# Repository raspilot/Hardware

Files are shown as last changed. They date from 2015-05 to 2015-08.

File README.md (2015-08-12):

#树莓派飞控RasPilot#

###RasPilot硬件参数###
特性
* 支持树莓派1 A+/B+；树莓派2 B+
* STM32F103 failsafe co-processor
* ardupilot飞控代码
* pixhawk接口兼容
* USB(RPi) / Servo Rail BEC / Power Module三路电源输入

传感器
* ST Micro L3GD20H 16位陀螺仪
* ST Micro LSM303D 14位加速度计/磁力计
* Invensense MPU 6000 3轴陀螺仪/加速度计
* MEAS MS5611 气压计

接口
* 2x UART
* 1x CAN
* 8x PWM
* Spektrum DSM / DSM2 / DSM-X® Satellite 兼容接收机
* Futaba S.BUS® 兼容输入输出
* PPM sum 接收机
* RSSI（PWM或电压）输入
* 1x I2C
* 3.3V & 6.6V A/D输入
* 安全开关
* 蜂鸣器接口
* 板载三色LED

###硬件安装和接线###
1 安装外壳。如下图，用铜柱和螺母将树莓派固定在底壳上。插上飞控扩展板，再用螺丝固定上壳。<br>

<br>
<br>
2 接口说明：<br>
<br>

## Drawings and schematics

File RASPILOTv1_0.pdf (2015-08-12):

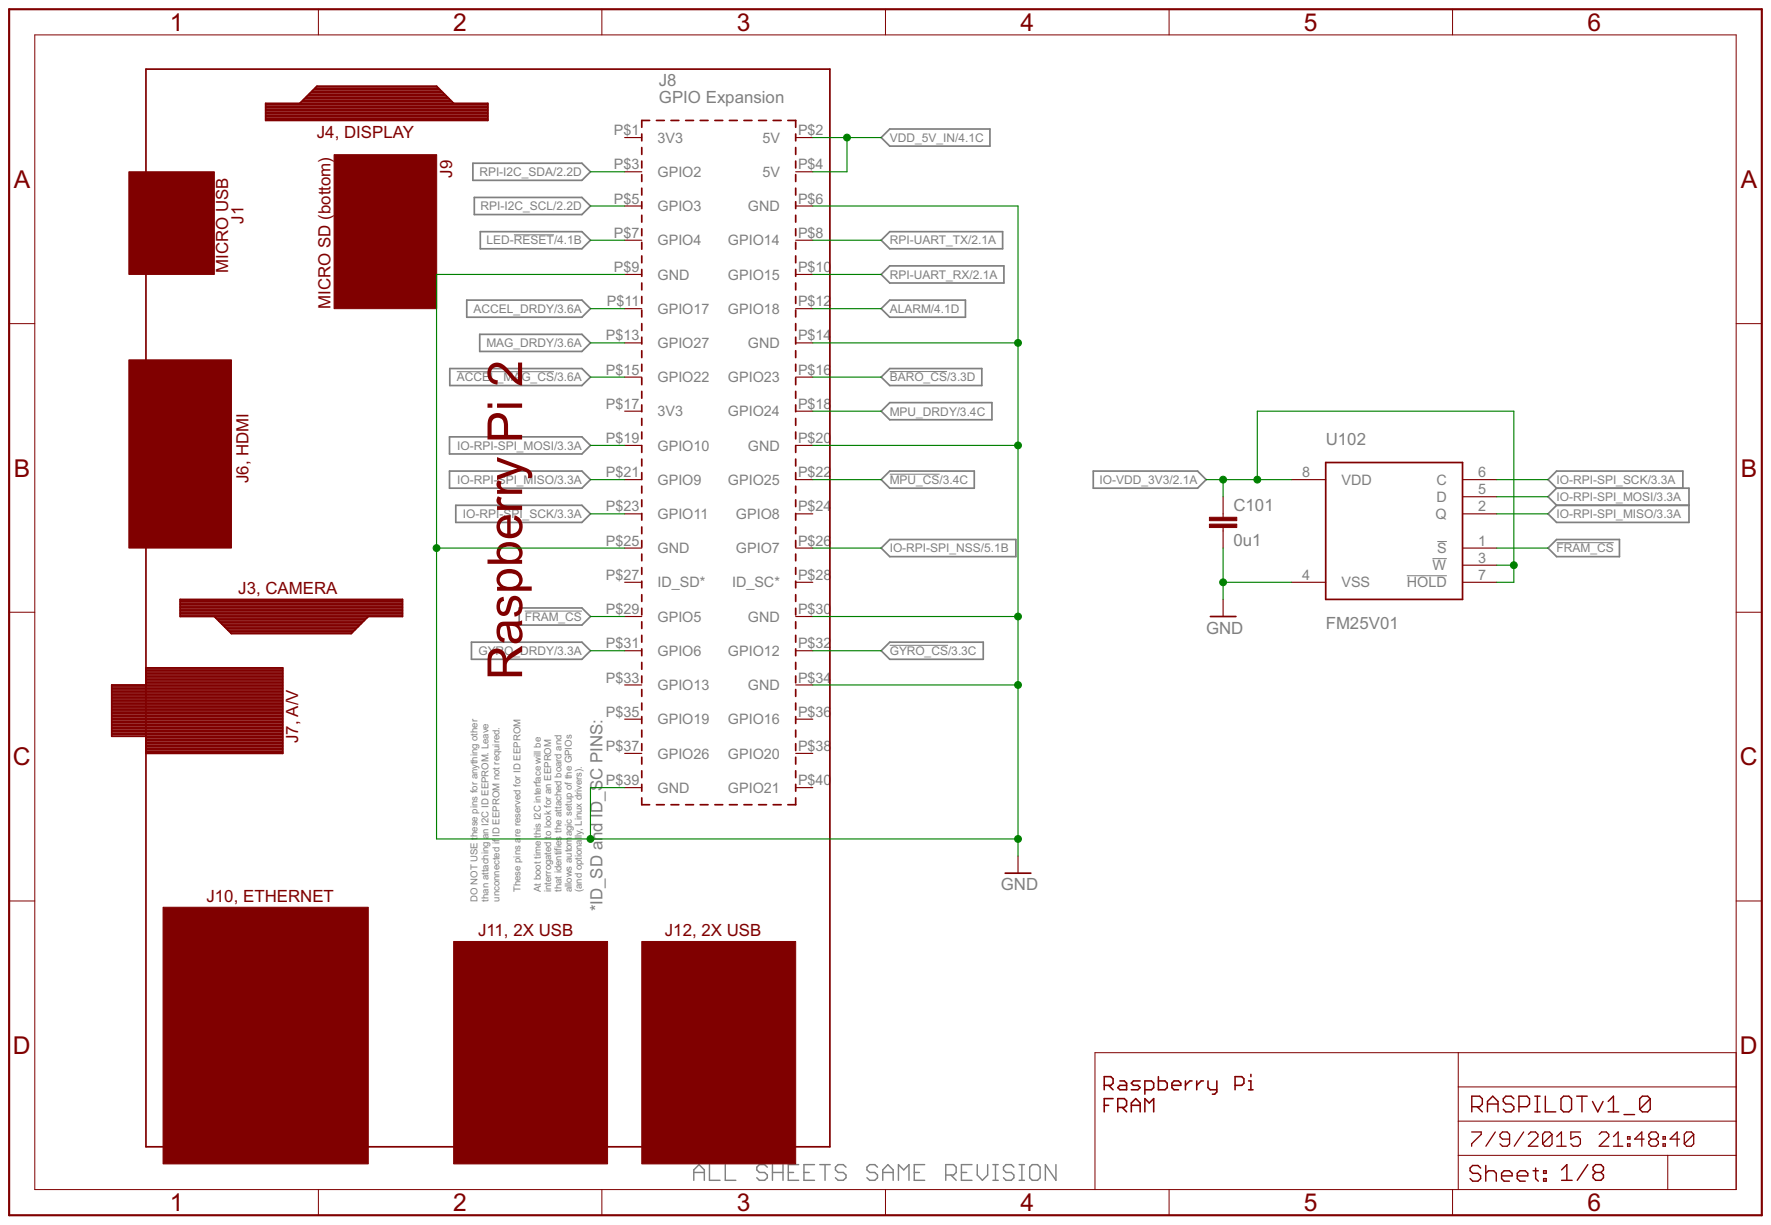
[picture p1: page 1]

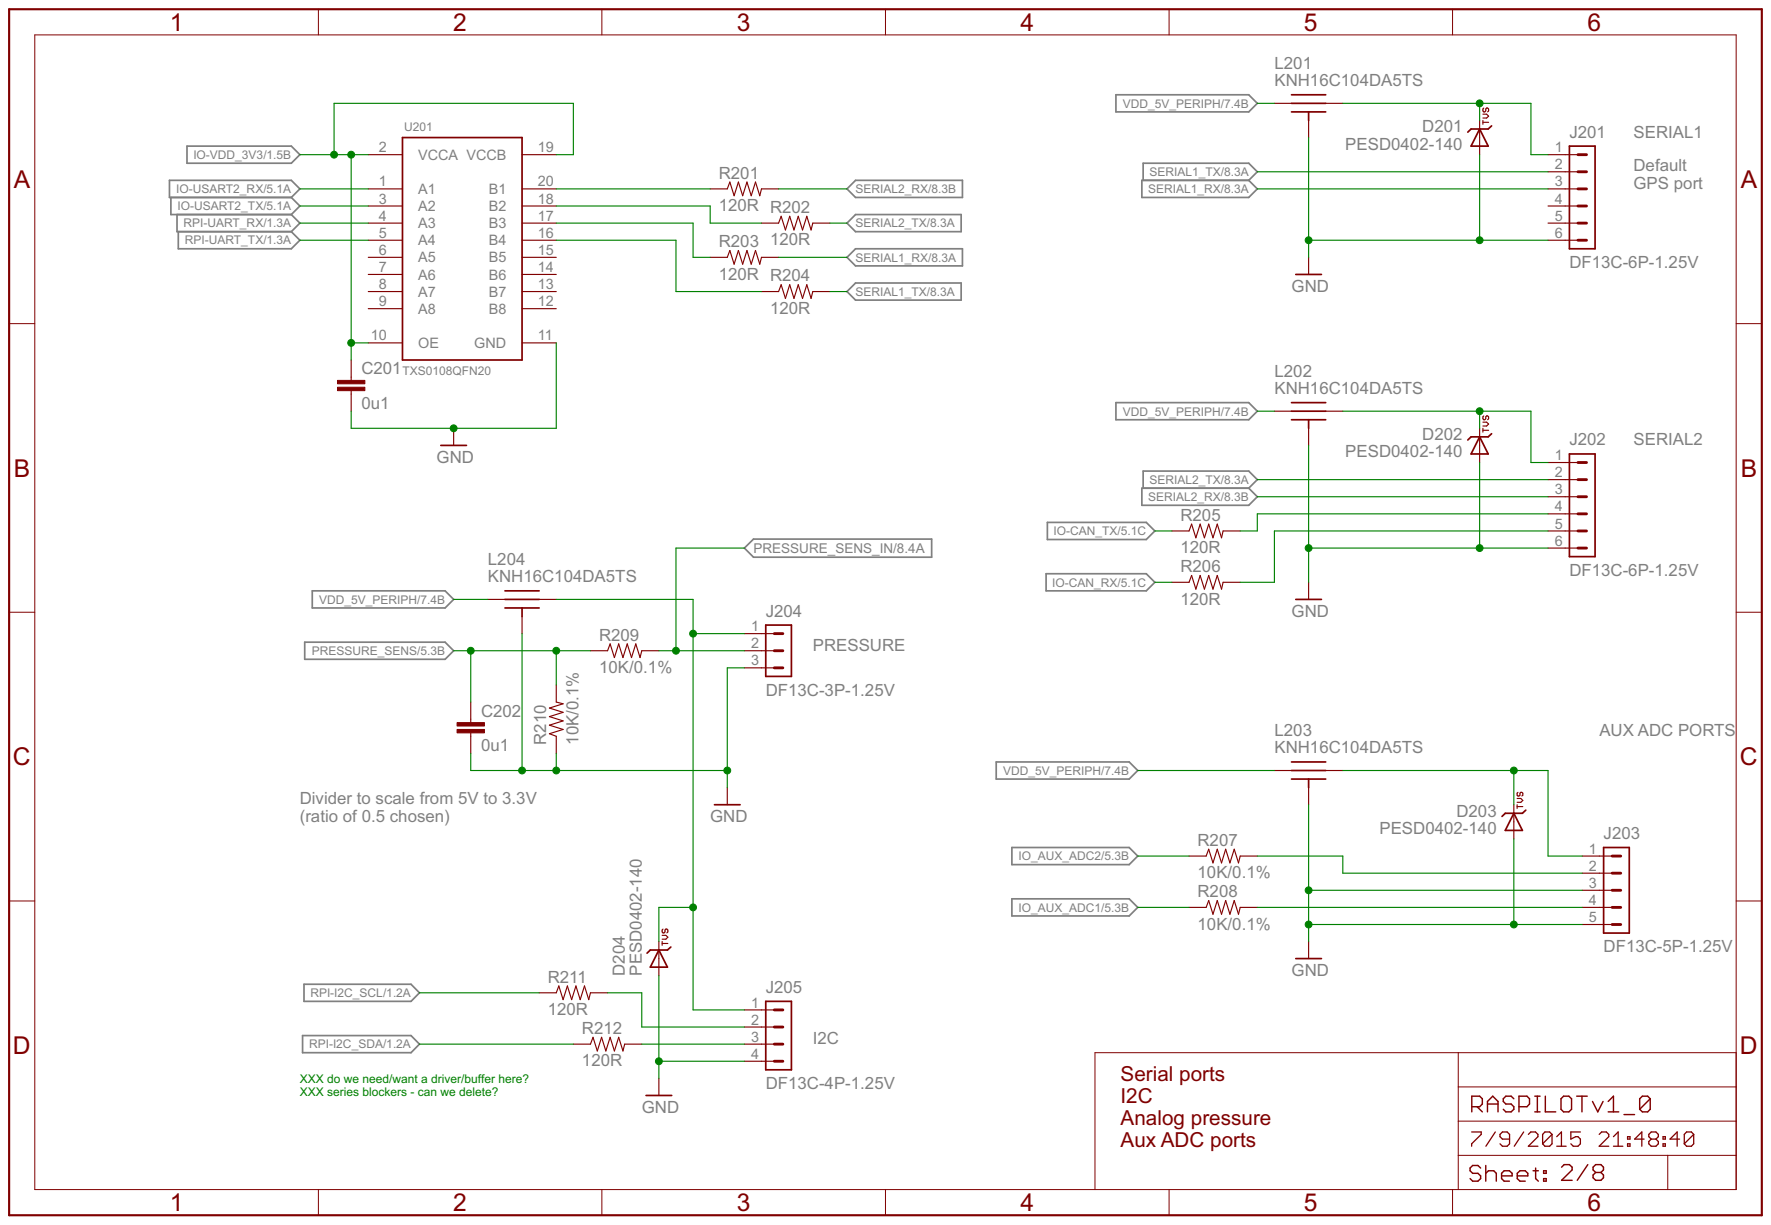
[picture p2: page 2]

Divider to scale from 5V to 3.3V
(ratio of 0.5 chosen)

XXX do we need/want a driver/buffer here? XXX series blockers - can we delete?

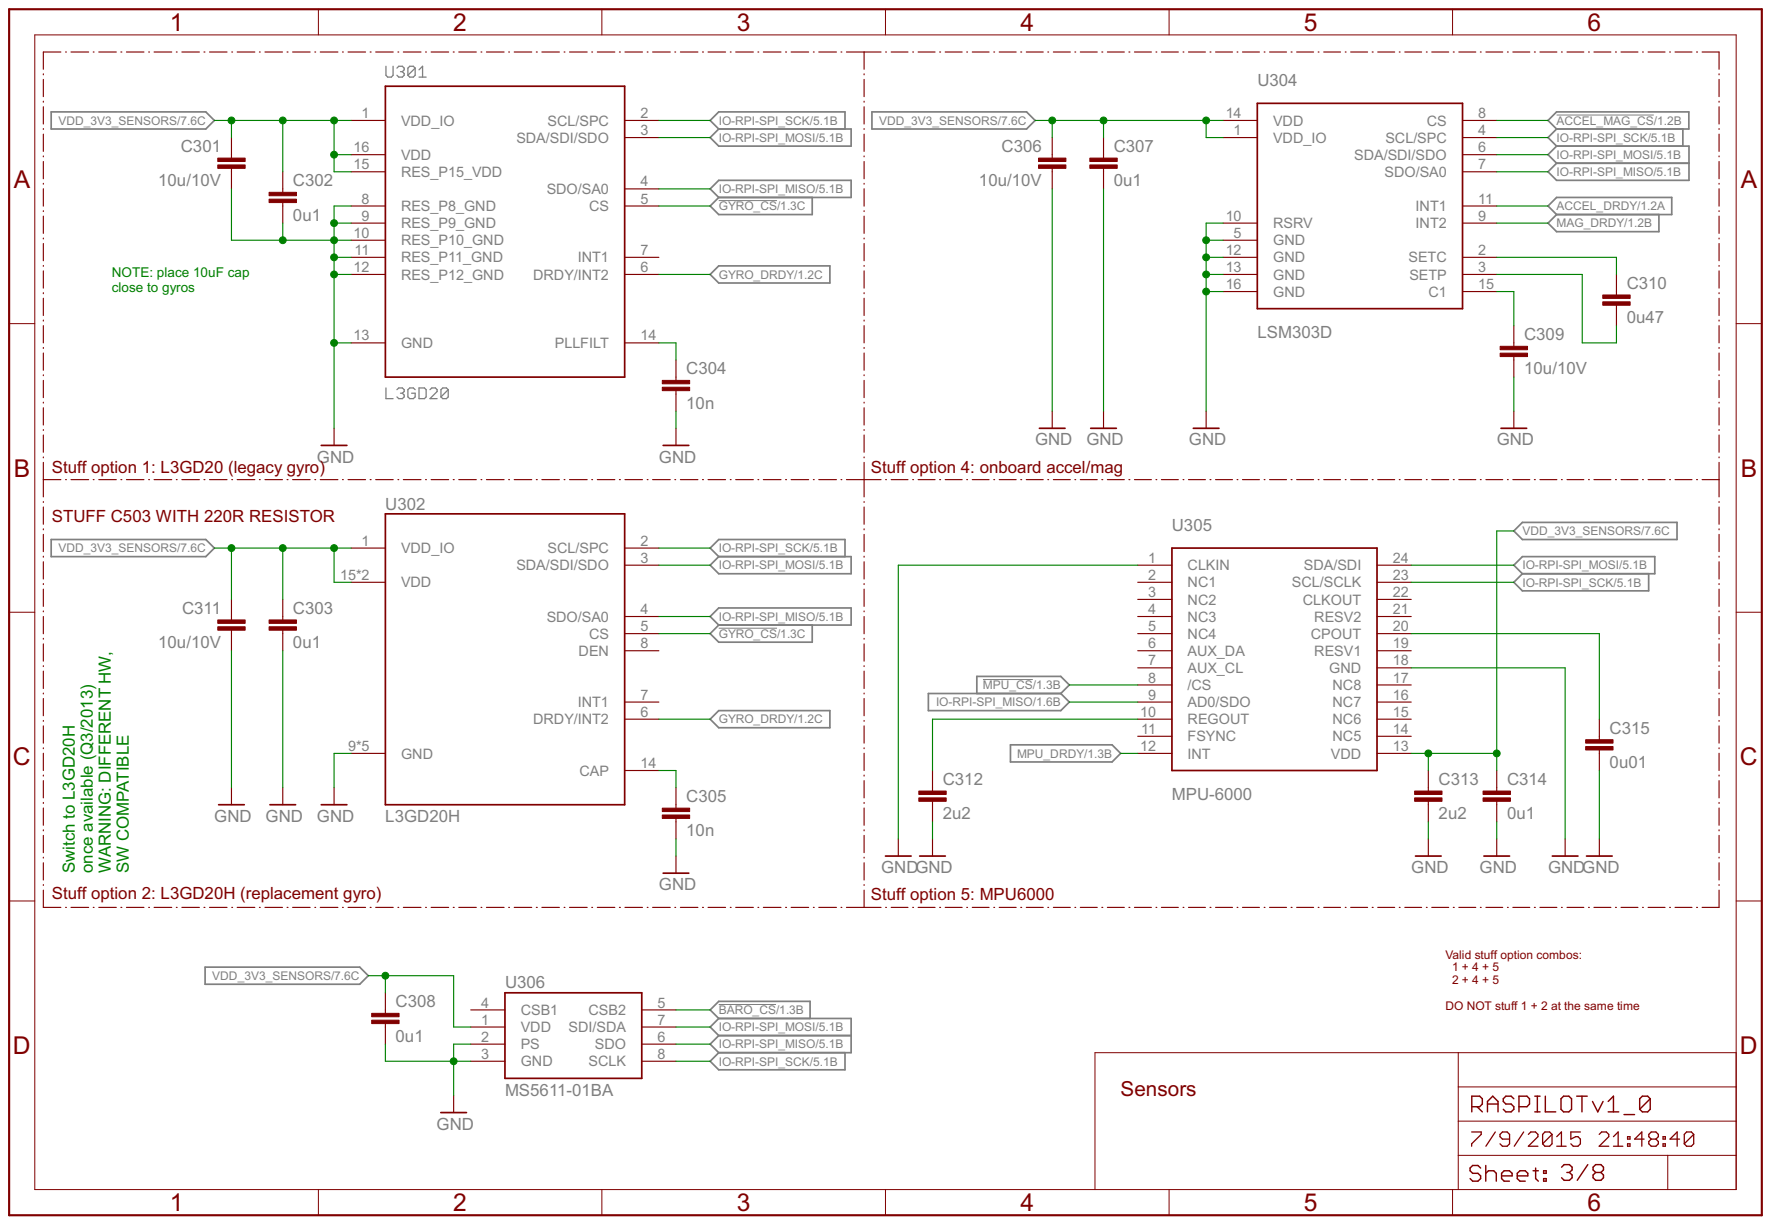
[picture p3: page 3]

Stuff option 1: L3GD20 (legacy gyro)

Stuff option 4: onboard accel/mag

19 CPOUT 18 RESV1

once available (Q3/2013) WARNING: DIFFERENT HW, SW CO

17 GND 16 NC8 15 NC7 14 NC6 13 NC5

Stuff option 2: L3GD20H (replacement gyro)

Valid stuff option combos: 1 + 4 + 5

2 + 4 + 5 DO NOT stuff 1 + 2 at the same time

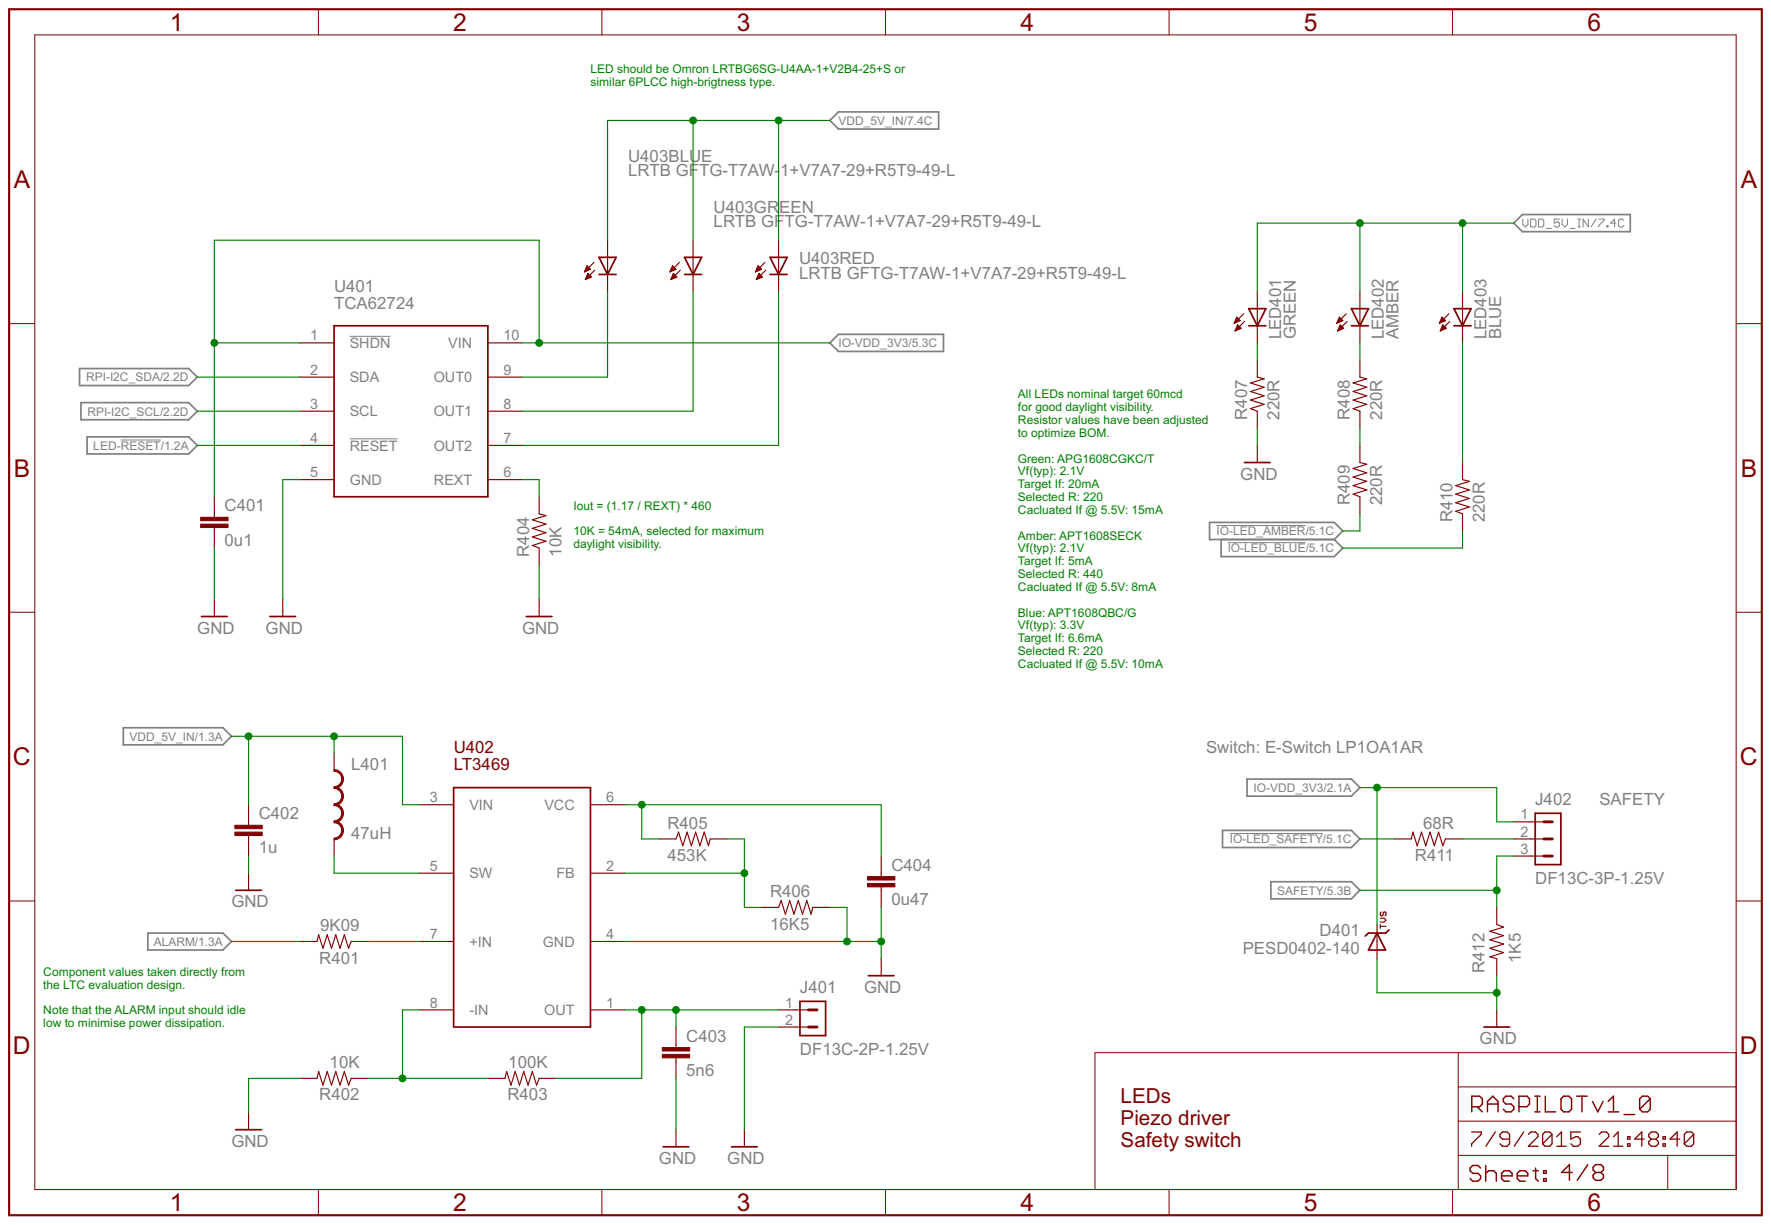
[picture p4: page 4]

LED should be Omron LRTBG6SG-U4AA-1+V2B4-25+S or similar 6PLCC high-brigtness type.

All LEDs nominal target 60mcd
for good daylight visibility. Resistor values have been adjusted

to optimize BOM. Green: APG1608CGKC/T Vf(typ): 2.1V

Component values taken directly from
the LTC evaluation design. Note that the ALARM input should idle

low to minimise power dissipation.

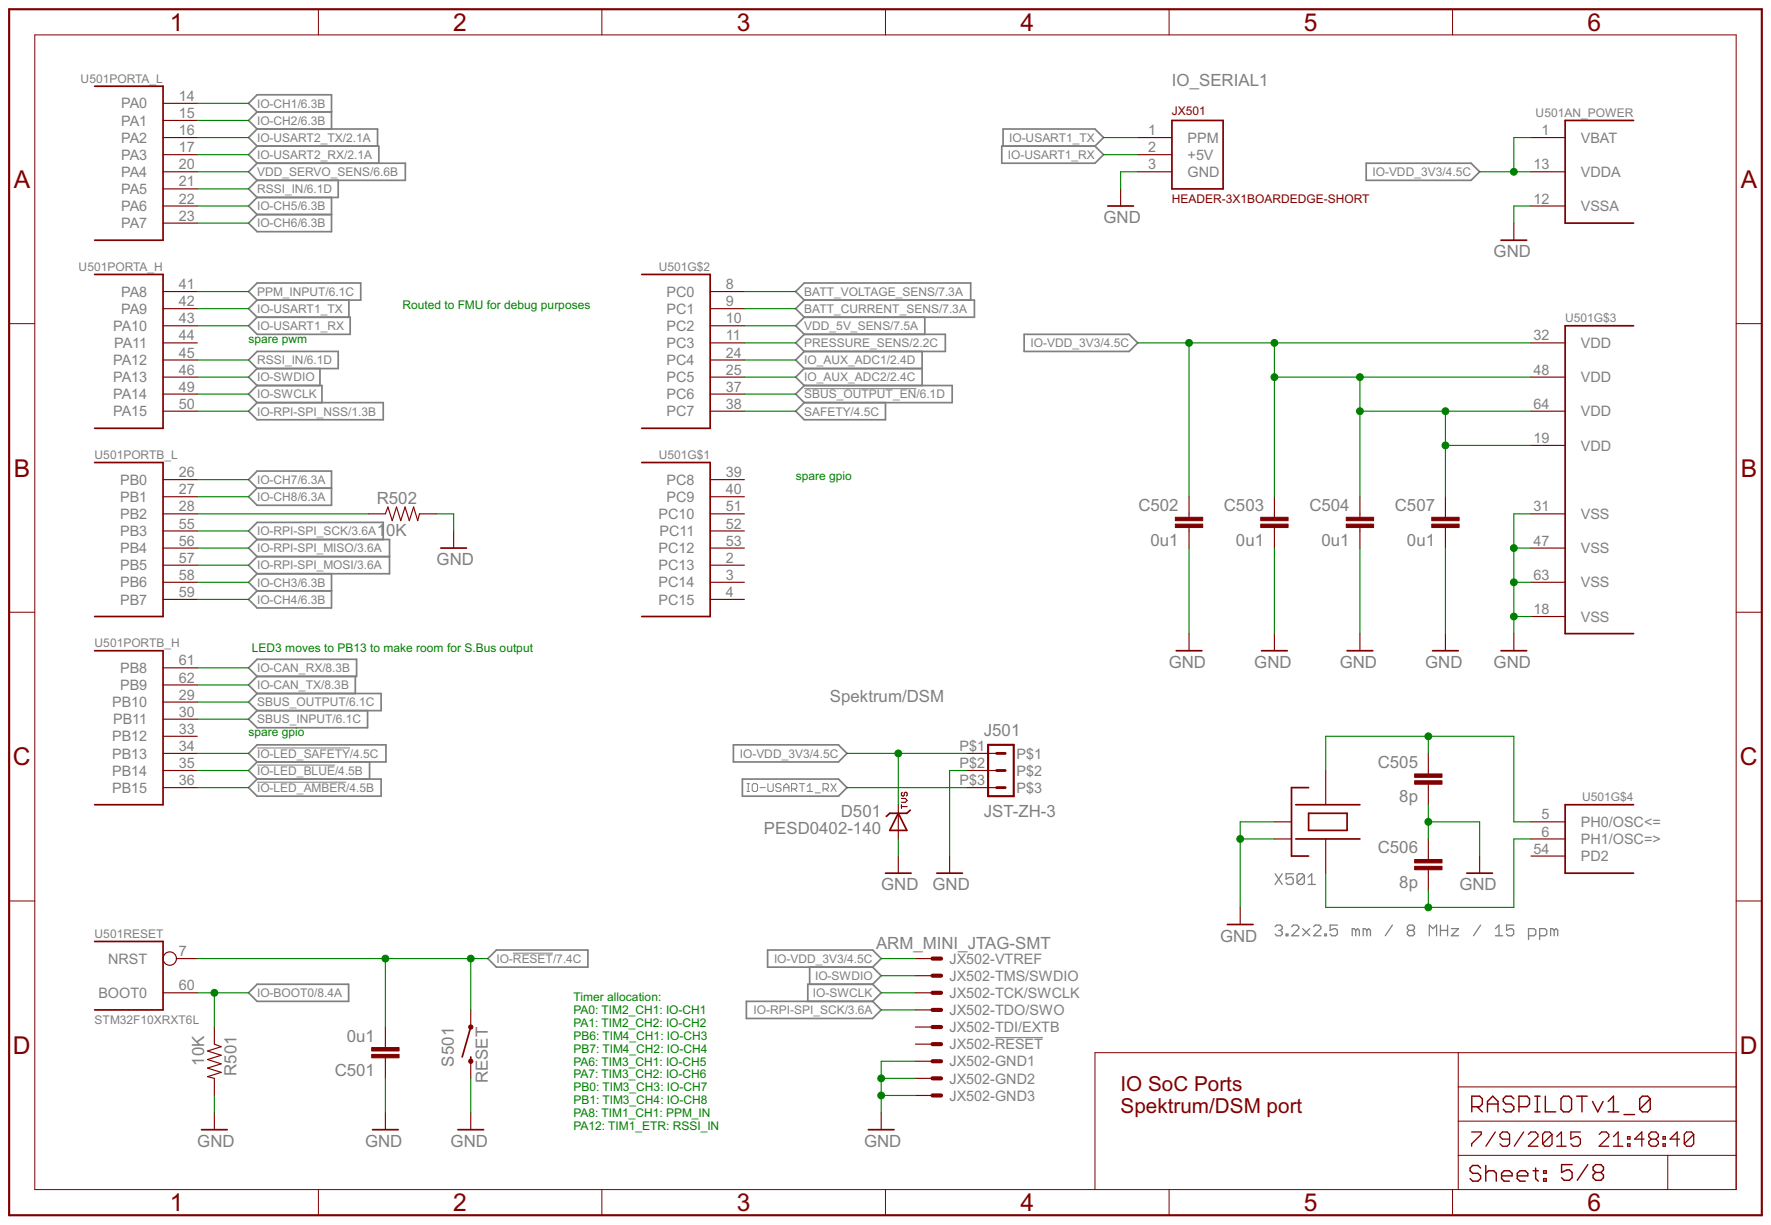
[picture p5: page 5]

Routed to FMU for debug purposes

LED3 moves to PB13 to make room for S.Bus output
IO-CAN_RX/8.3B
IO-CAN_TX/8.3B
SBUS_OUTPUT/6.1C
SBUS_INPUT/6.1C
spare gpio

Timer allocation: PA0: TIM2_CH1: IO-CH1 PA1: TIM2_CH2: IO-CH2 PB6: TIM4_CH1: IO-CH3 PB7: TIM4_CH2: IO-CH4 PA6: TIM3_CH1: IO-CH5 PA7: TIM3_CH2: IO-CH6 PB0: TIM3_CH3: IO-CH7 PB1: TIM3_CH4: IO-CH8 PA8: TIM1_CH1: PPM_IN

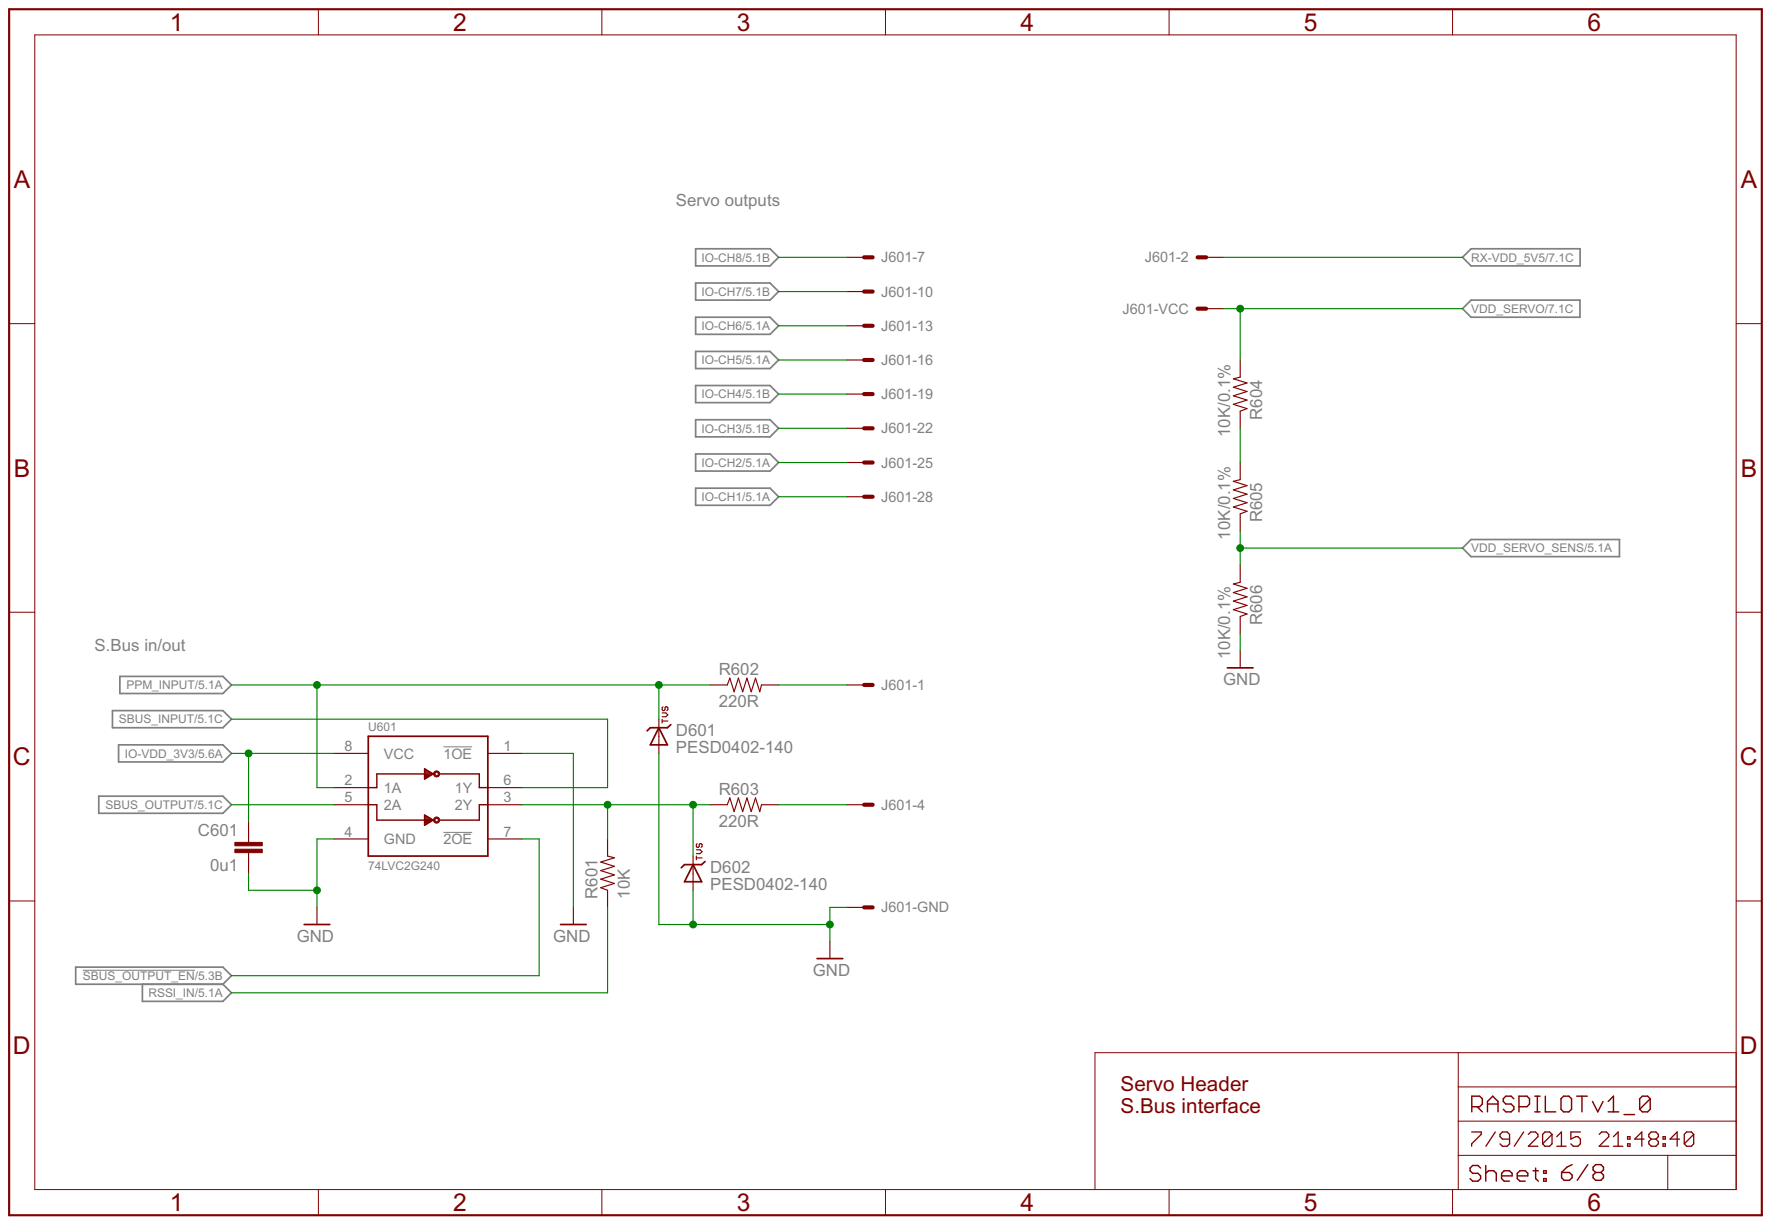
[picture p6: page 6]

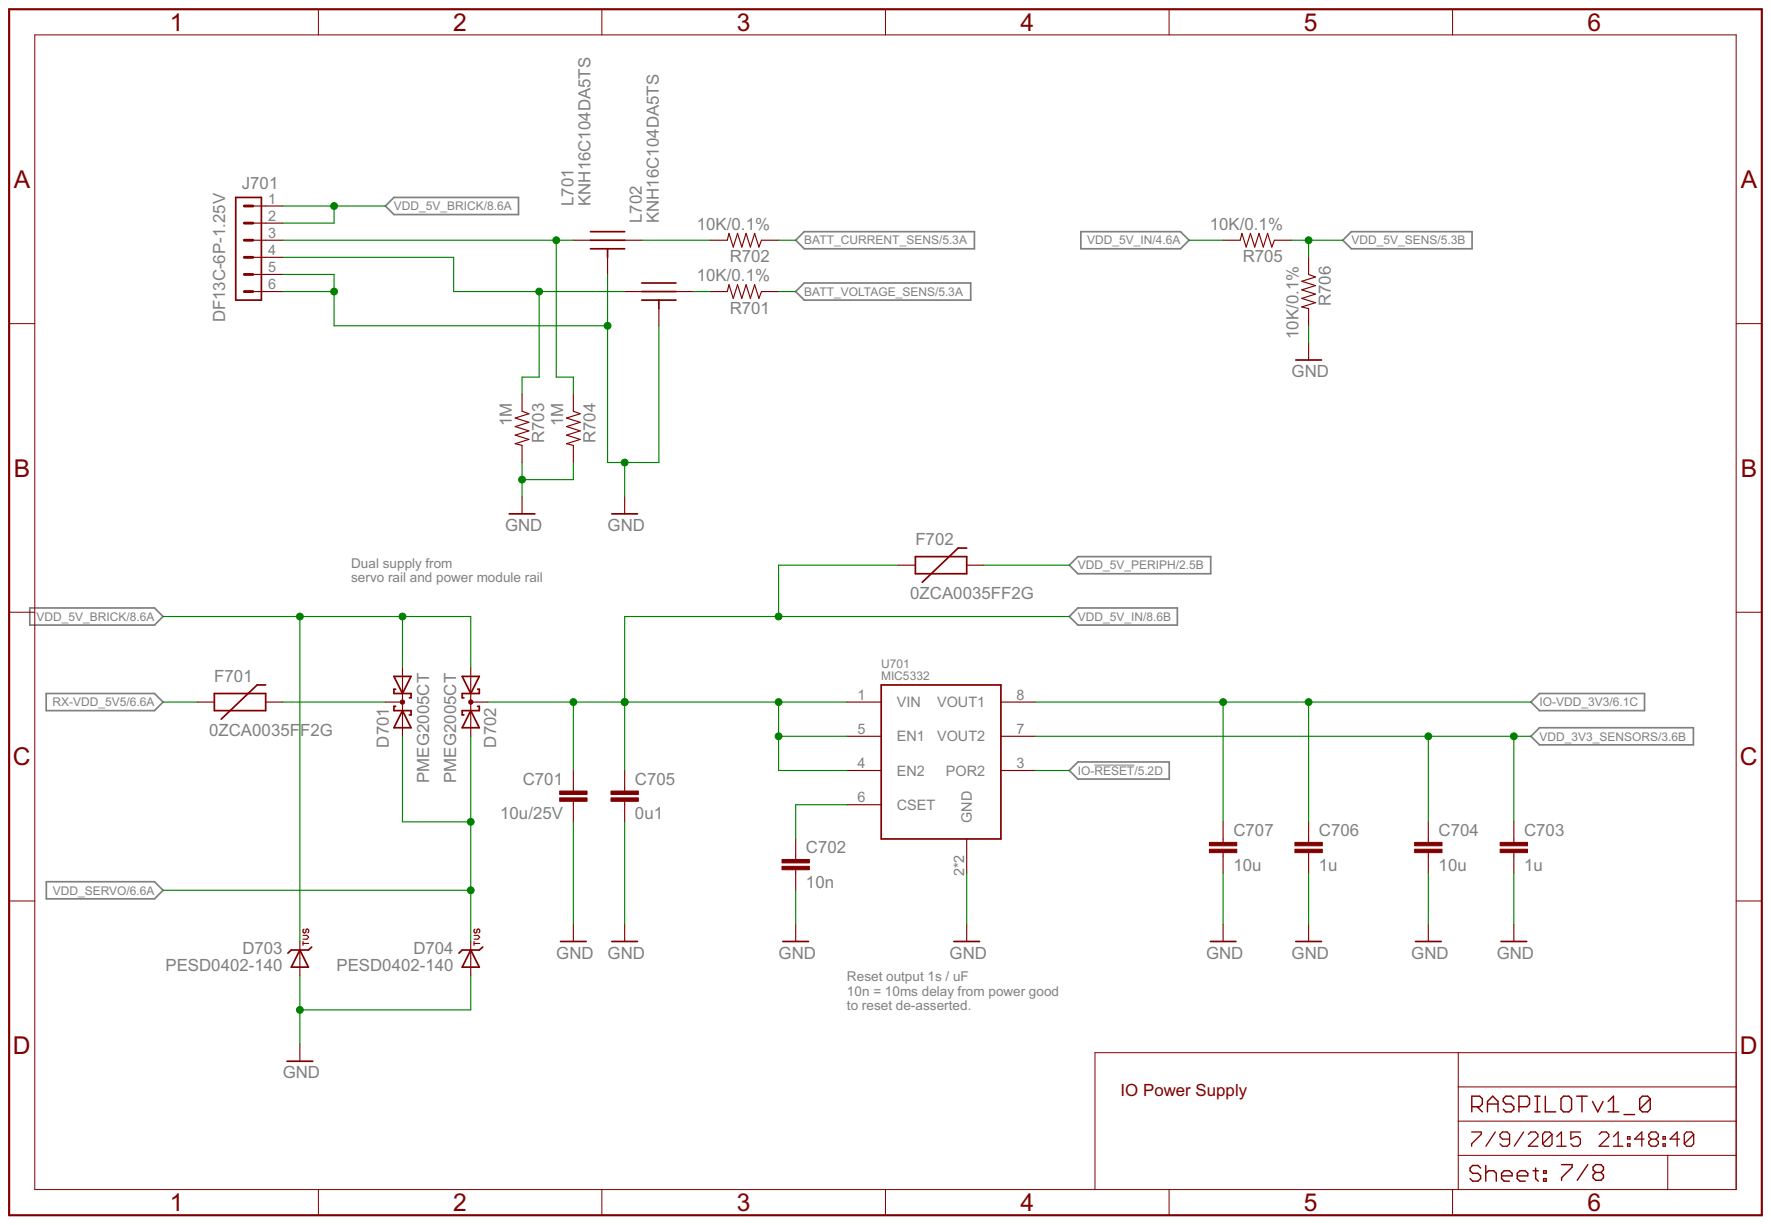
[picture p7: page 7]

Dual supply from
servo rail and power module rail

Reset output 1s / uF
10n = 10ms delay from power good
to reset de-asserted.

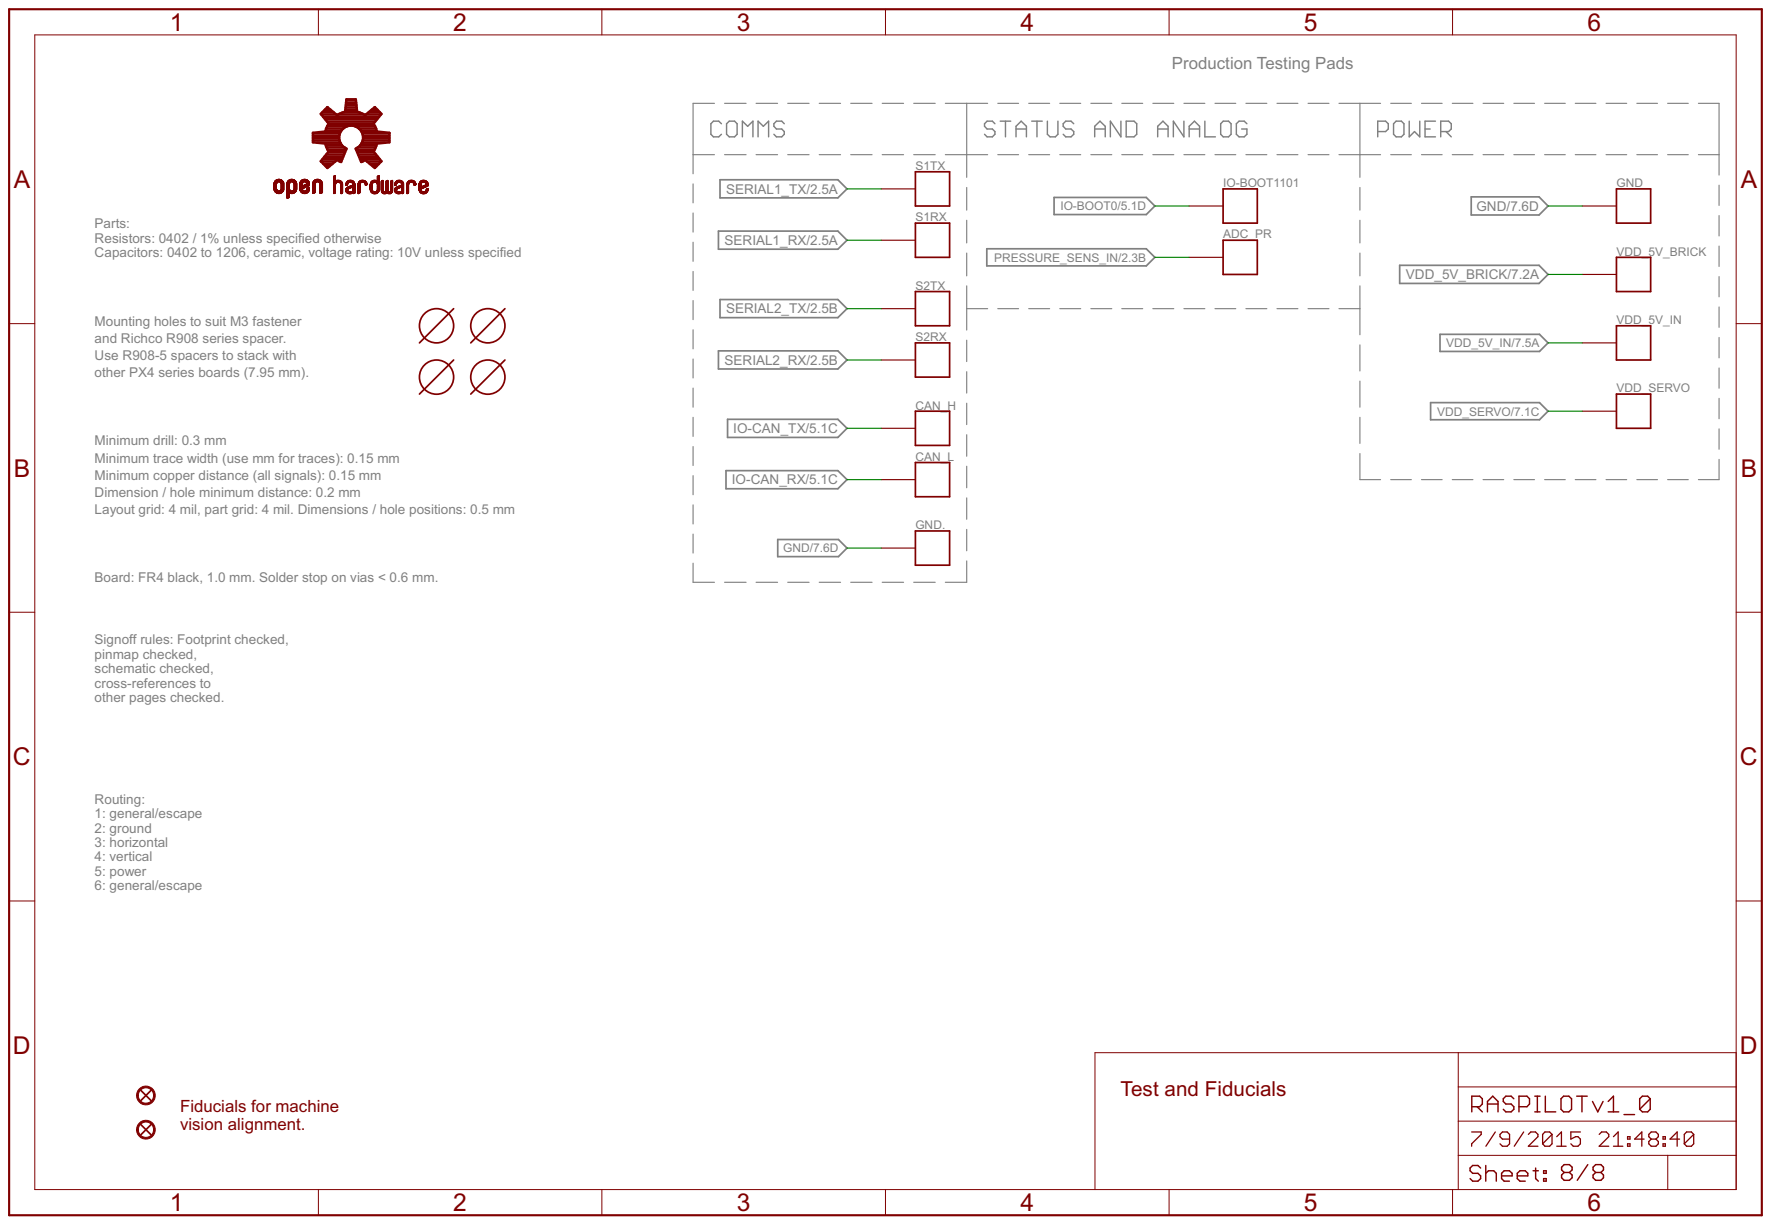
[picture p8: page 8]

Parts: Resistors: 0402 / 1% unless specified otherwise Capacitors: 0402 to 1206, ceramic, voltage rating: 10V unless specified

Mounting holes to suit M3 fastener and Richco R908 series spacer. Use R908-5 spacers to stack with

other PX4 series boards (7.95 mm).

Minimum drill: 0.3 mm
Minimum trace width (use mm for traces): 0.15 mm
Minimum copper distance (all signals): 0.15 mm
Dimension / hole minimum distance: 0.2 mm
Layout grid: 4 mil, part grid: 4 mil. Dimensions / hole positions: 0.5 mm

Board: FR4 black, 1.0 mm. Solder stop on vias < 0.6 mm. Signoff rules: Footprint checked, pinmap checked, schematic checked, cross-references to

other pages checked. Routing: 1: general/escape

2: ground
3: horizontal 4: vertical 5: power 6: general/escape

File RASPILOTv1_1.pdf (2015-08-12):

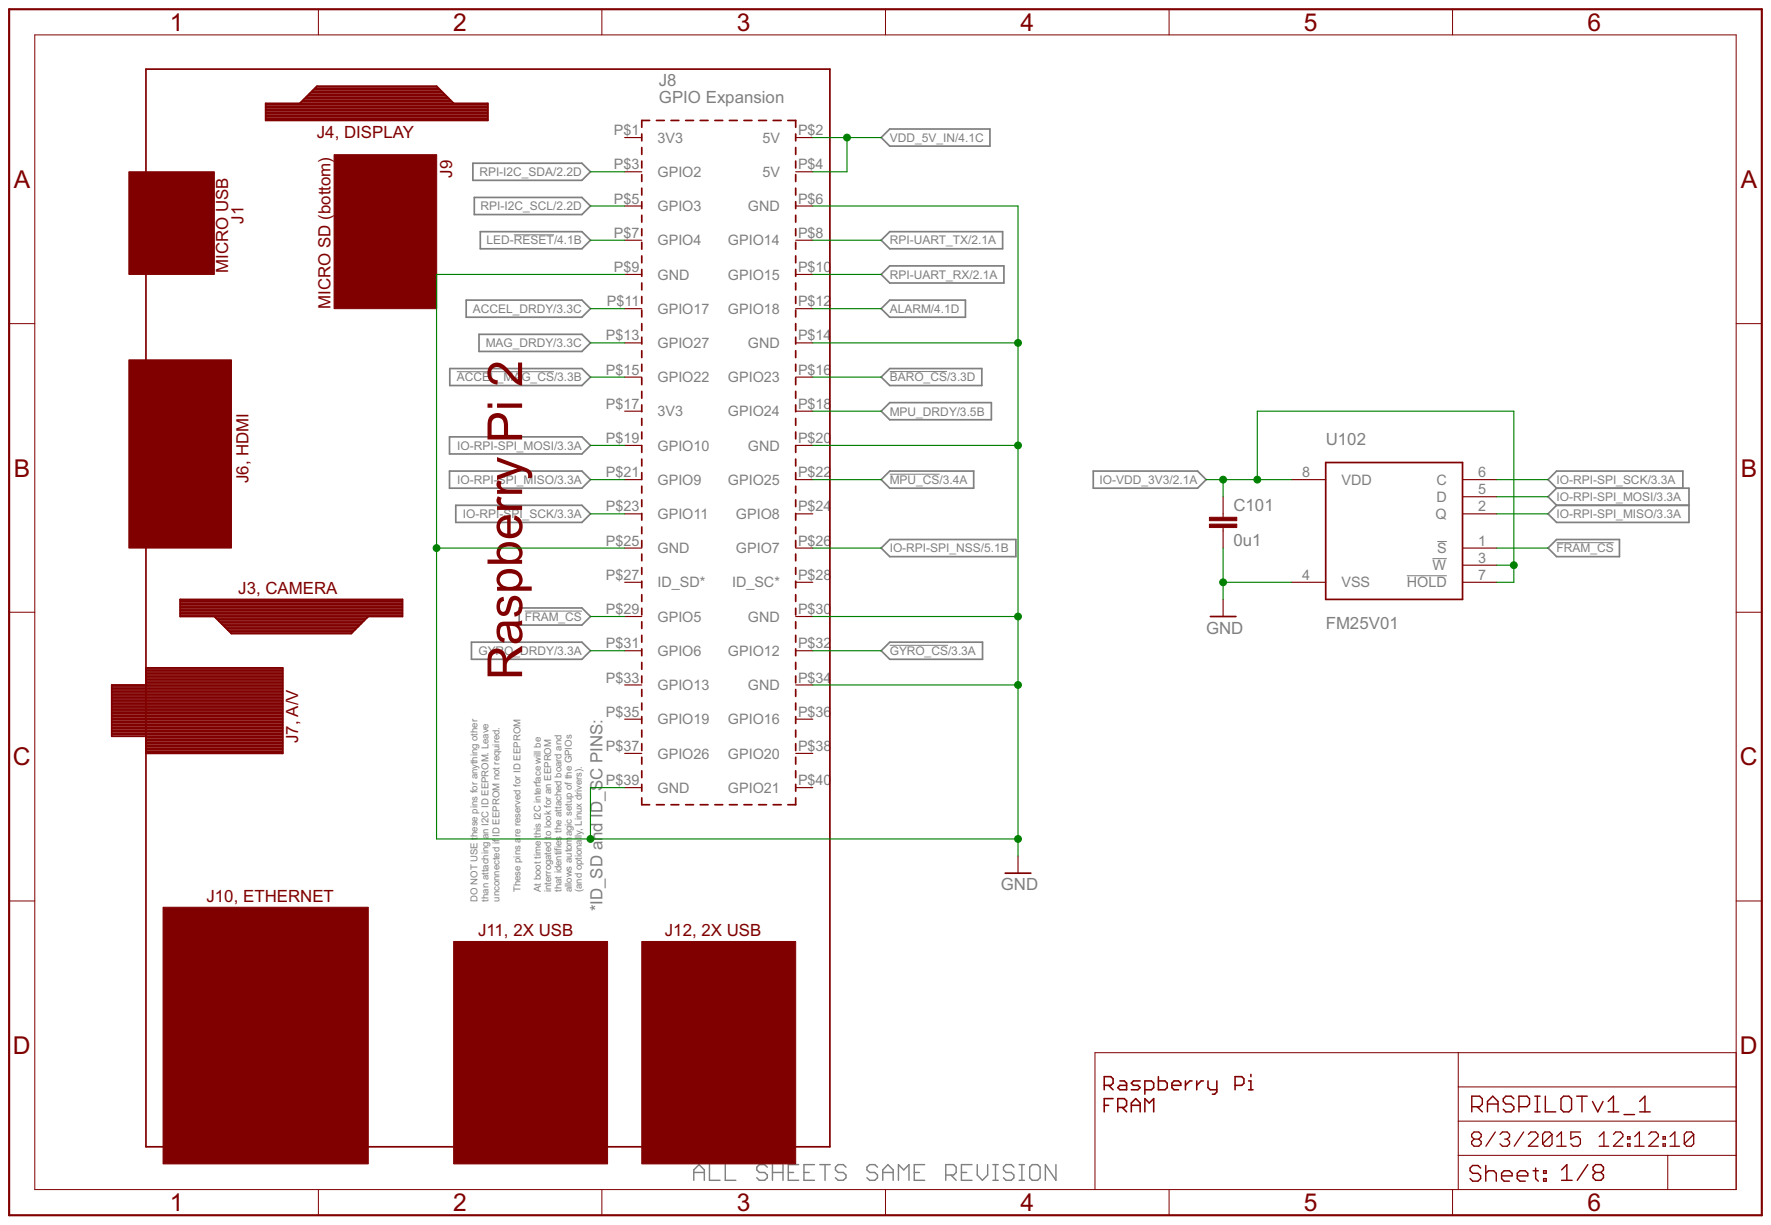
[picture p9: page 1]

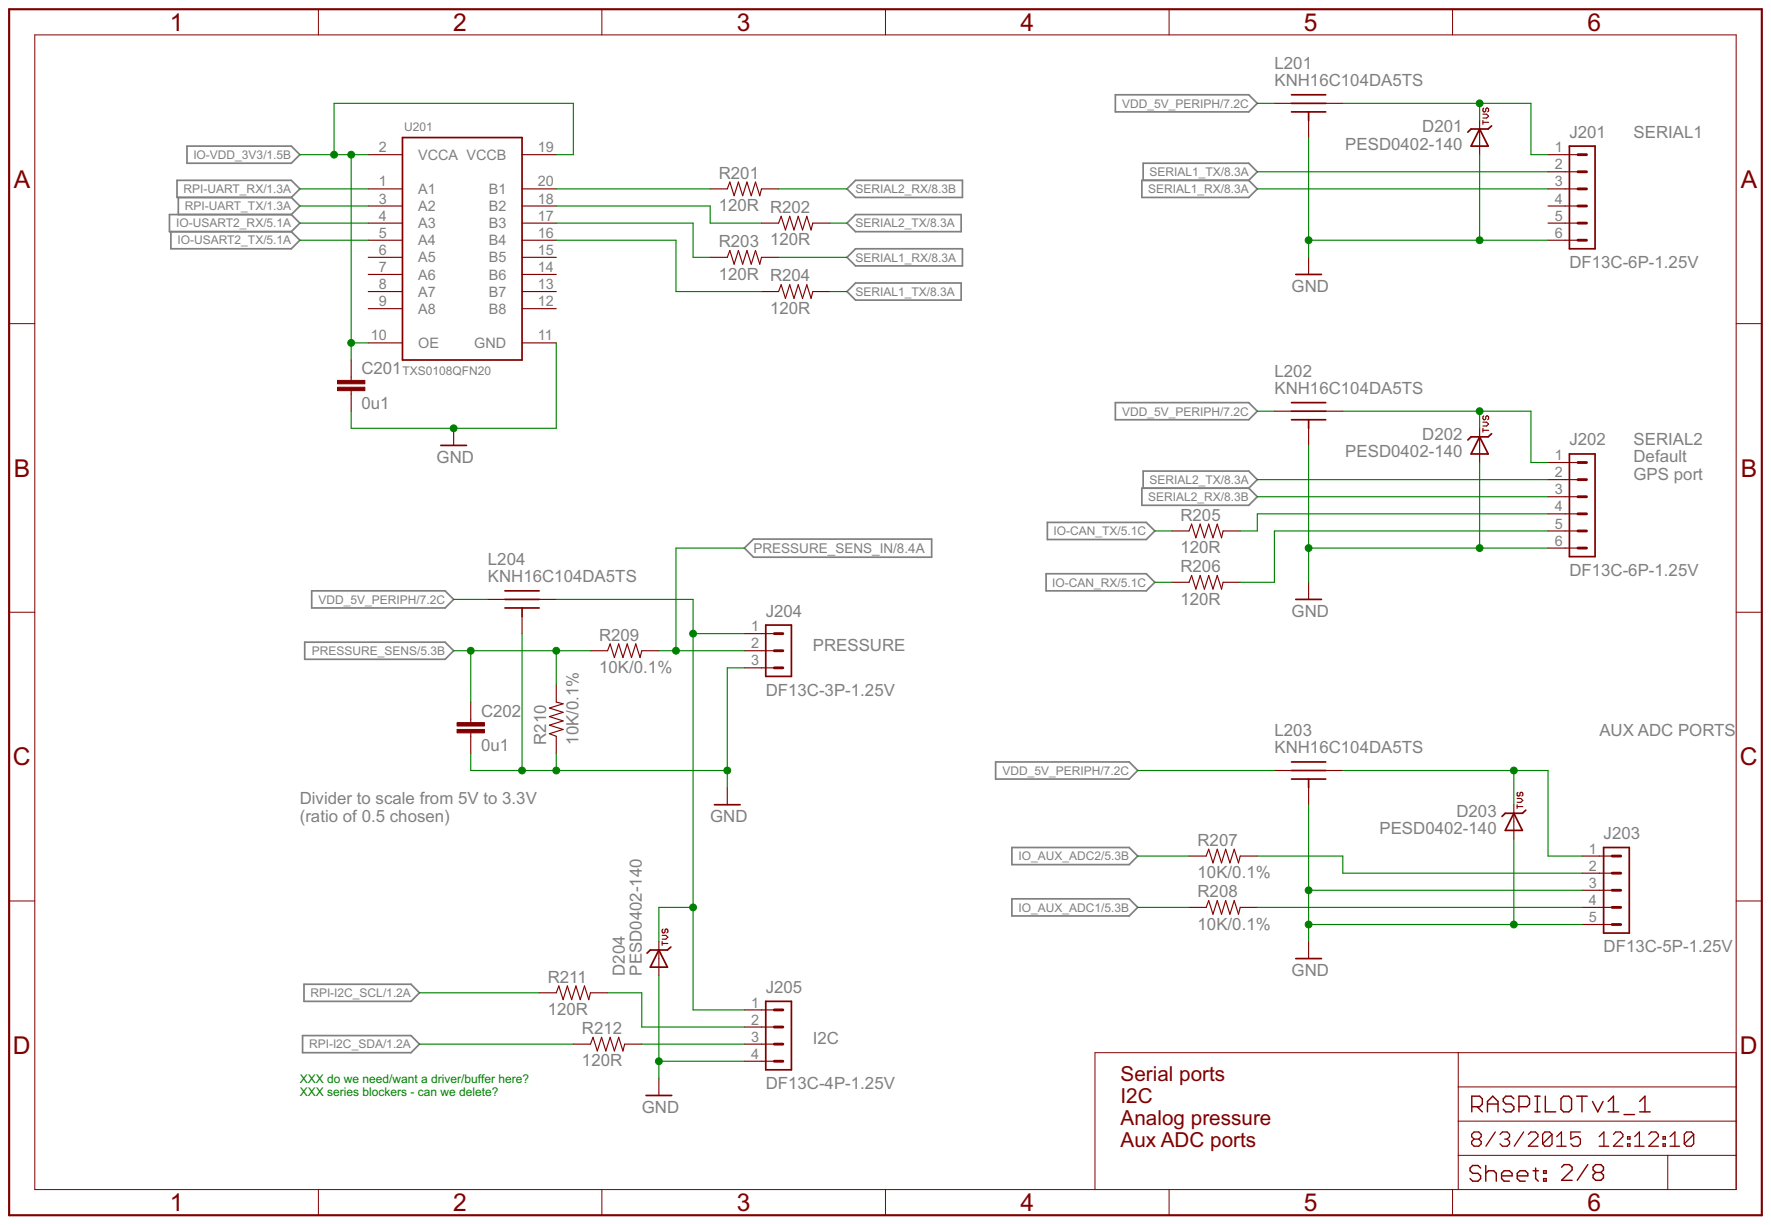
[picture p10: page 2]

Divider to scale from 5V to 3.3V
(ratio of 0.5 chosen)

XXX do we need/want a driver/buffer here? XXX series blockers - can we delete?

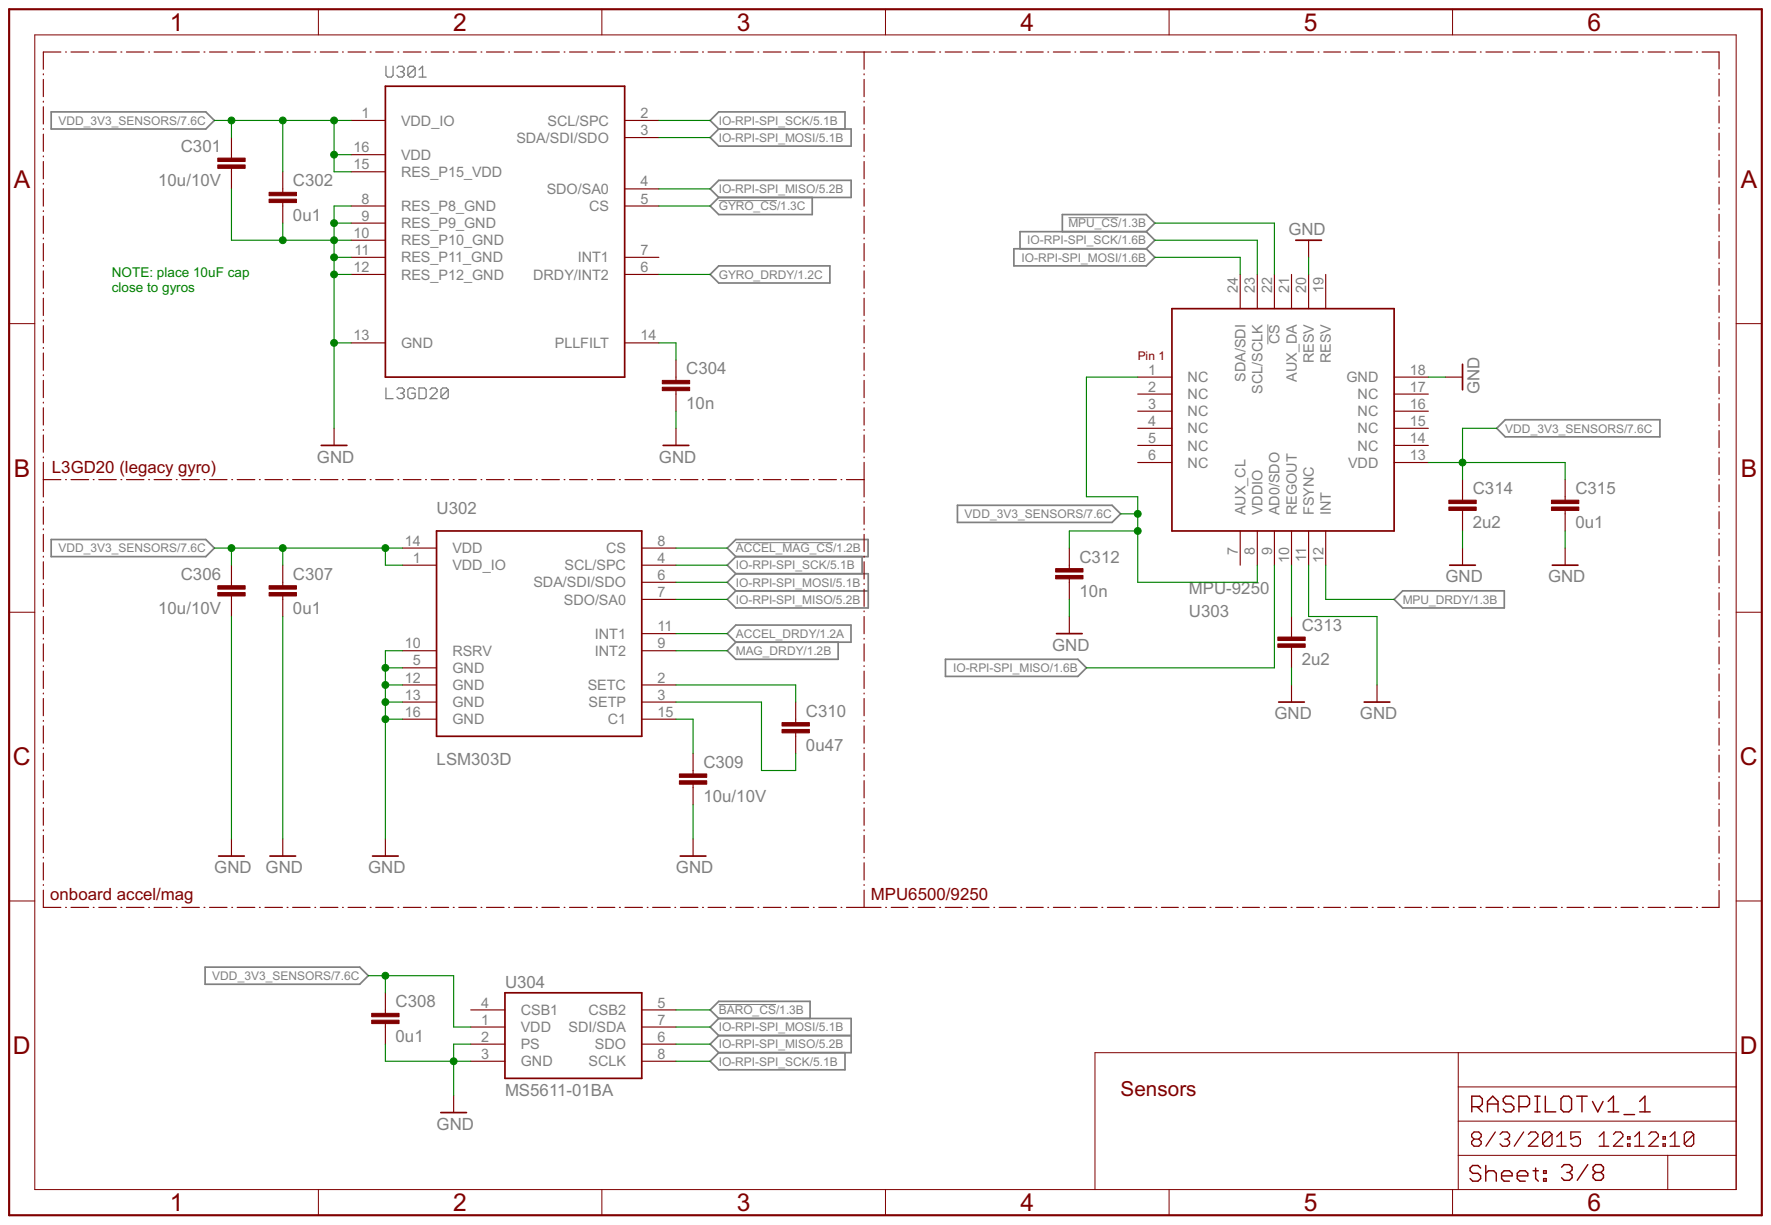
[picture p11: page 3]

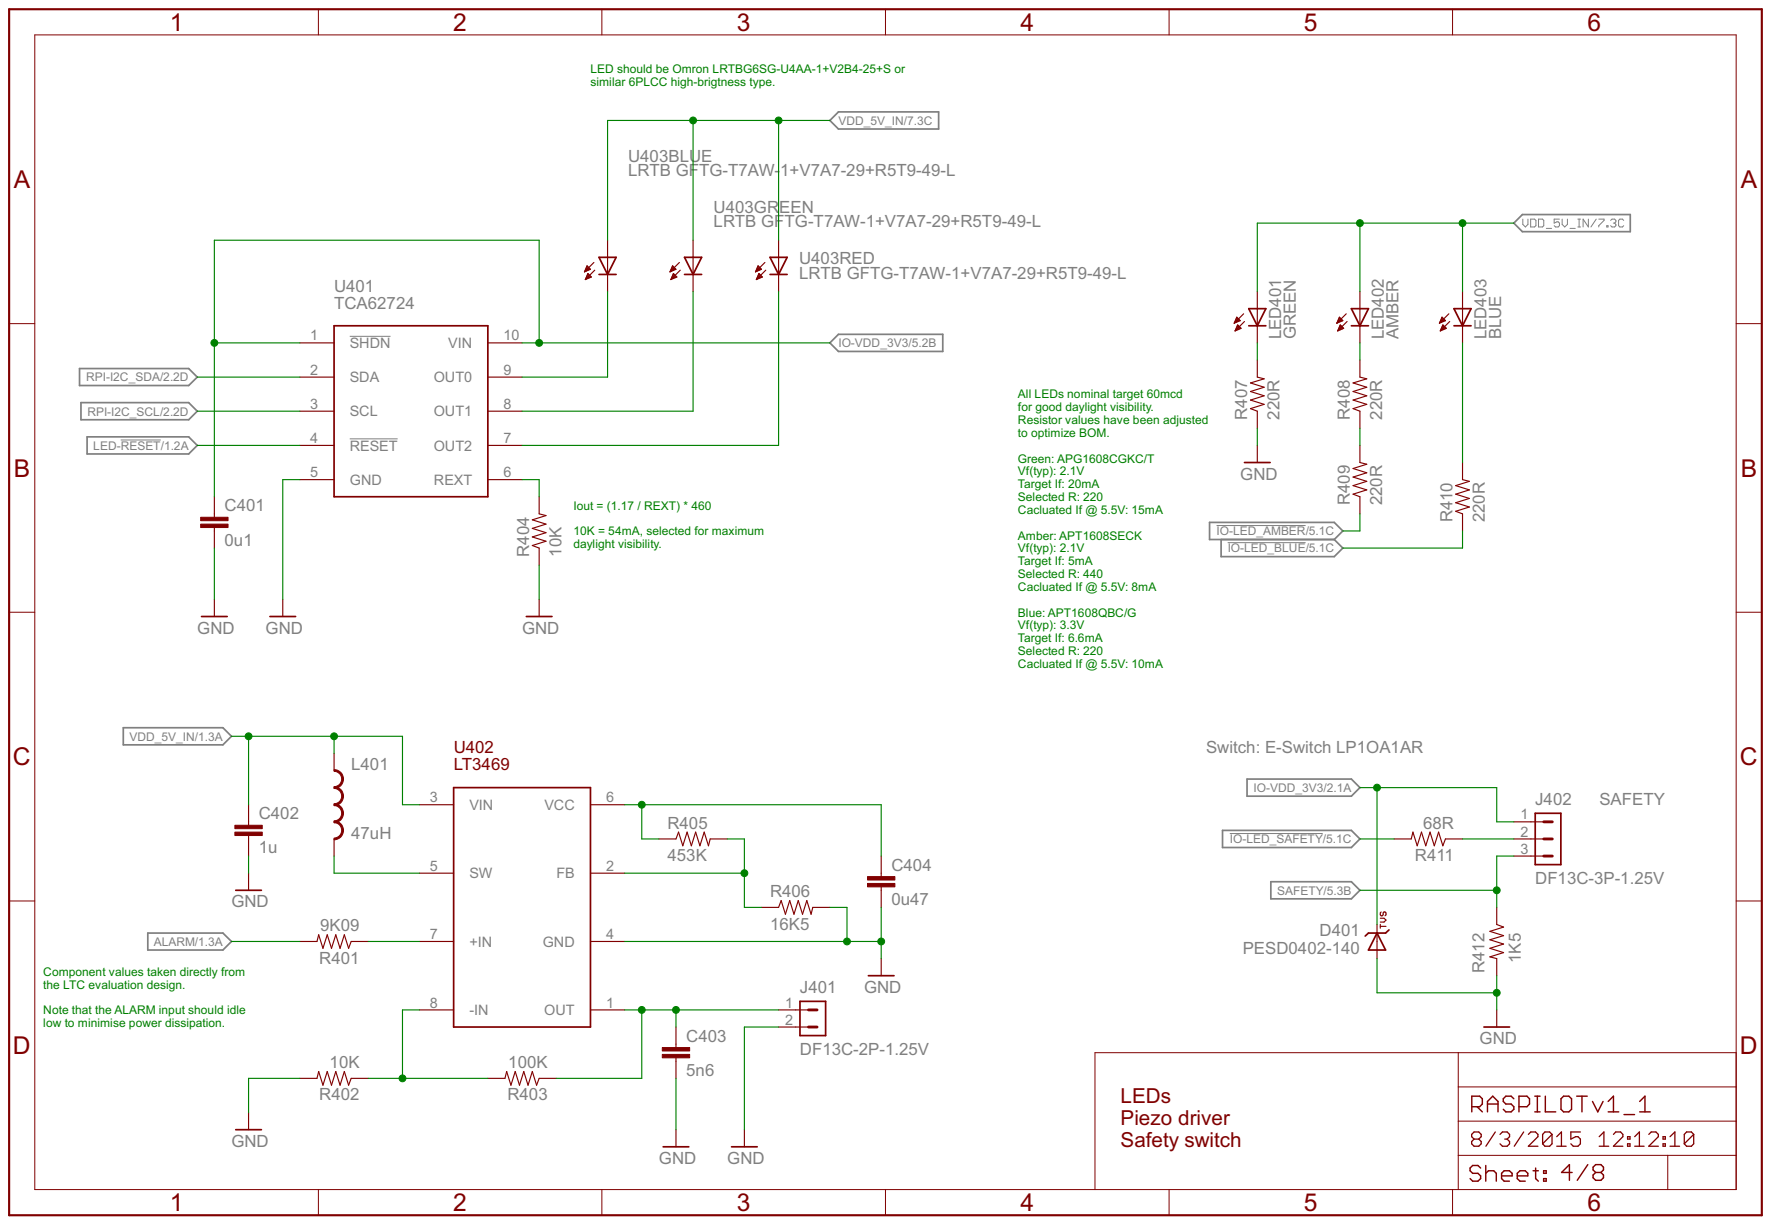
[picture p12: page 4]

LED should be Omron LRTBG6SG-U4AA-1+V2B4-25+S or similar 6PLCC high-brigtness type.

All LEDs nominal target 60mcd
for good daylight visibility. Resistor values have been adjusted

to optimize BOM. Green: APG1608CGKC/T Vf(typ): 2.1V

Component values taken directly from
the LTC evaluation design. Note that the ALARM input should idle

low to minimise power dissipation.


Routed to FMU for debug purposes

LED3 moves to PB13 to make room for S.Bus output
IO-CAN_RX/8.3B
IO-CAN_TX/8.3B
SBUS_OUTPUT/6.1C
SBUS_INPUT/6.1C
spare gpio

Timer allocation: PA0: TIM2_CH1: IO-CH1 PA1: TIM2_CH2: IO-CH2 PB6: TIM4_CH1: IO-CH3 PB7: TIM4_CH2: IO-CH4 PA6: TIM3_CH1: IO-CH5 PA7: TIM3_CH2: IO-CH6 PB0: TIM3_CH3: IO-CH7 PB1: TIM3_CH4: IO-CH8 PA8: TIM1_CH1: PPM_IN



Dual supply from
servo rail and power module rail

Reset output 1s / uF
10n = 10ms delay from power good
to reset de-asserted.


Parts: Resistors: 0402 / 1% unless specified otherwise Capacitors: 0402 to 1206, ceramic, voltage rating: 10V unless specified

Mounting holes to suit M3 fastener and Richco R908 series spacer. Use R908-5 spacers to stack with

other PX4 series boards (7.95 mm).

Minimum drill: 0.3 mm
Minimum trace width (use mm for traces): 0.15 mm
Minimum copper distance (all signals): 0.15 mm
Dimension / hole minimum distance: 0.2 mm
Layout grid: 4 mil, part grid: 4 mil. Dimensions / hole positions: 0.5 mm

Board: FR4 black, 1.0 mm. Solder stop on vias < 0.6 mm. Signoff rules: Footprint checked, pinmap checked, schematic checked, cross-references to

other pages checked. Routing: 1: general/escape

2: ground
3: horizontal 4: vertical 5: power 6: general/escape

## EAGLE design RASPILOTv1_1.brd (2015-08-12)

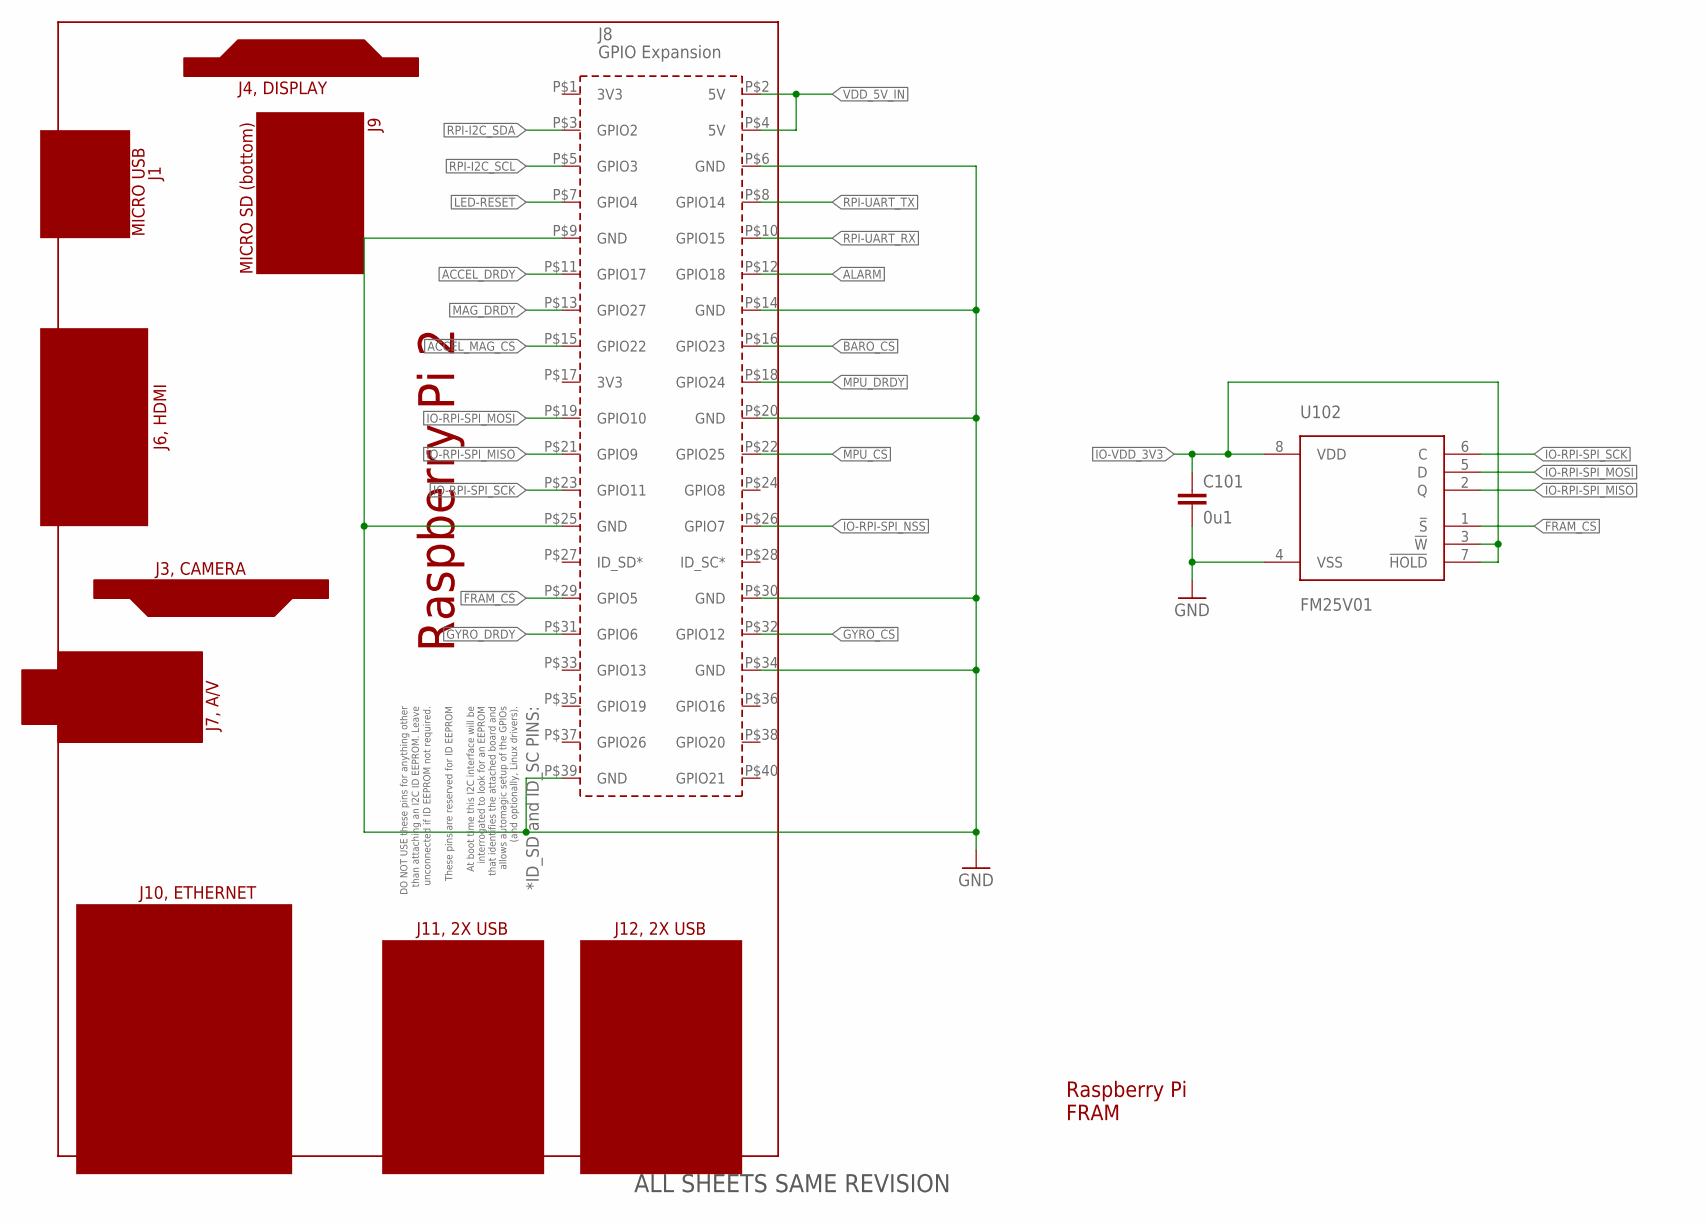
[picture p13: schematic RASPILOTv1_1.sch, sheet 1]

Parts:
C101: 0u1; 0402-CAP; PARTNO CC0402ZRY5V7BB104
U101: RPI2
U102: FM25V01; SO08; PARTNO FM25V01-G

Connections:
!ACCEL_MAG_CS: U101.P$15 (GPIO22); also elsewhere on the board
!BARO_CS: U101.P$16 (GPIO23); also elsewhere on the board
!FRAM_CS: U101.P$29 (GPIO5), U102.1 (!S)
!GYRO_CS: U101.P$32 (GPIO12); also elsewhere on the board
!MPU_CS: U101.P$22 (GPIO25); also elsewhere on the board
ACCEL_DRDY: U101.P$11 (GPIO17); also elsewhere on the board
ALARM: U101.P$12 (GPIO18); also elsewhere on the board
GND: C101.P$2 (2), U101.P$6 (GND), U101.P$9 (GND), U101.P$14 (GND), U101.P$20 (GND), U101.P$25 (GND), U101.P$30 (GND), U101.P$34 (GND), U101.P$39 (GND), U102.4 (VSS); also elsewhere on the board
GYRO_DRDY: U101.P$31 (GPIO6); also elsewhere on the board
IO-RPI-SPI_MISO: U101.P$21 (GPIO9), U102.2 (Q); also elsewhere on the board
IO-RPI-SPI_MOSI: U101.P$19 (GPIO10), U102.5 (D); also elsewhere on the board
IO-RPI-SPI_NSS: U101.P$26 (GPIO7); also elsewhere on the board
IO-RPI-SPI_SCK: U101.P$23 (GPIO11), U102.6 (C); also elsewhere on the board
IO-VDD_3V3: C101.P$1 (1), U102.3 (!W), U102.7 (!HOLD), U102.8 (VDD); also elsewhere on the board
LED-!RESET: U101.P$7 (GPIO4); also elsewhere on the board
MAG_DRDY: U101.P$13 (GPIO27); also elsewhere on the board
MPU_DRDY: U101.P$18 (GPIO24); also elsewhere on the board
RPI-I2C_SCL: U101.P$5 (GPIO3); also elsewhere on the board
RPI-I2C_SDA: U101.P$3 (GPIO2); also elsewhere on the board
RPI-UART_RX: U101.P$10 (GPIO15); also elsewhere on the board
RPI-UART_TX: U101.P$8 (GPIO14); also elsewhere on the board
VDD_5V_IN: U101.P$2 (5V), U101.P$4 (5V); also elsewhere on the board

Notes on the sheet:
Raspberry Pi FRAM
ALL SHEETS SAME REVISION

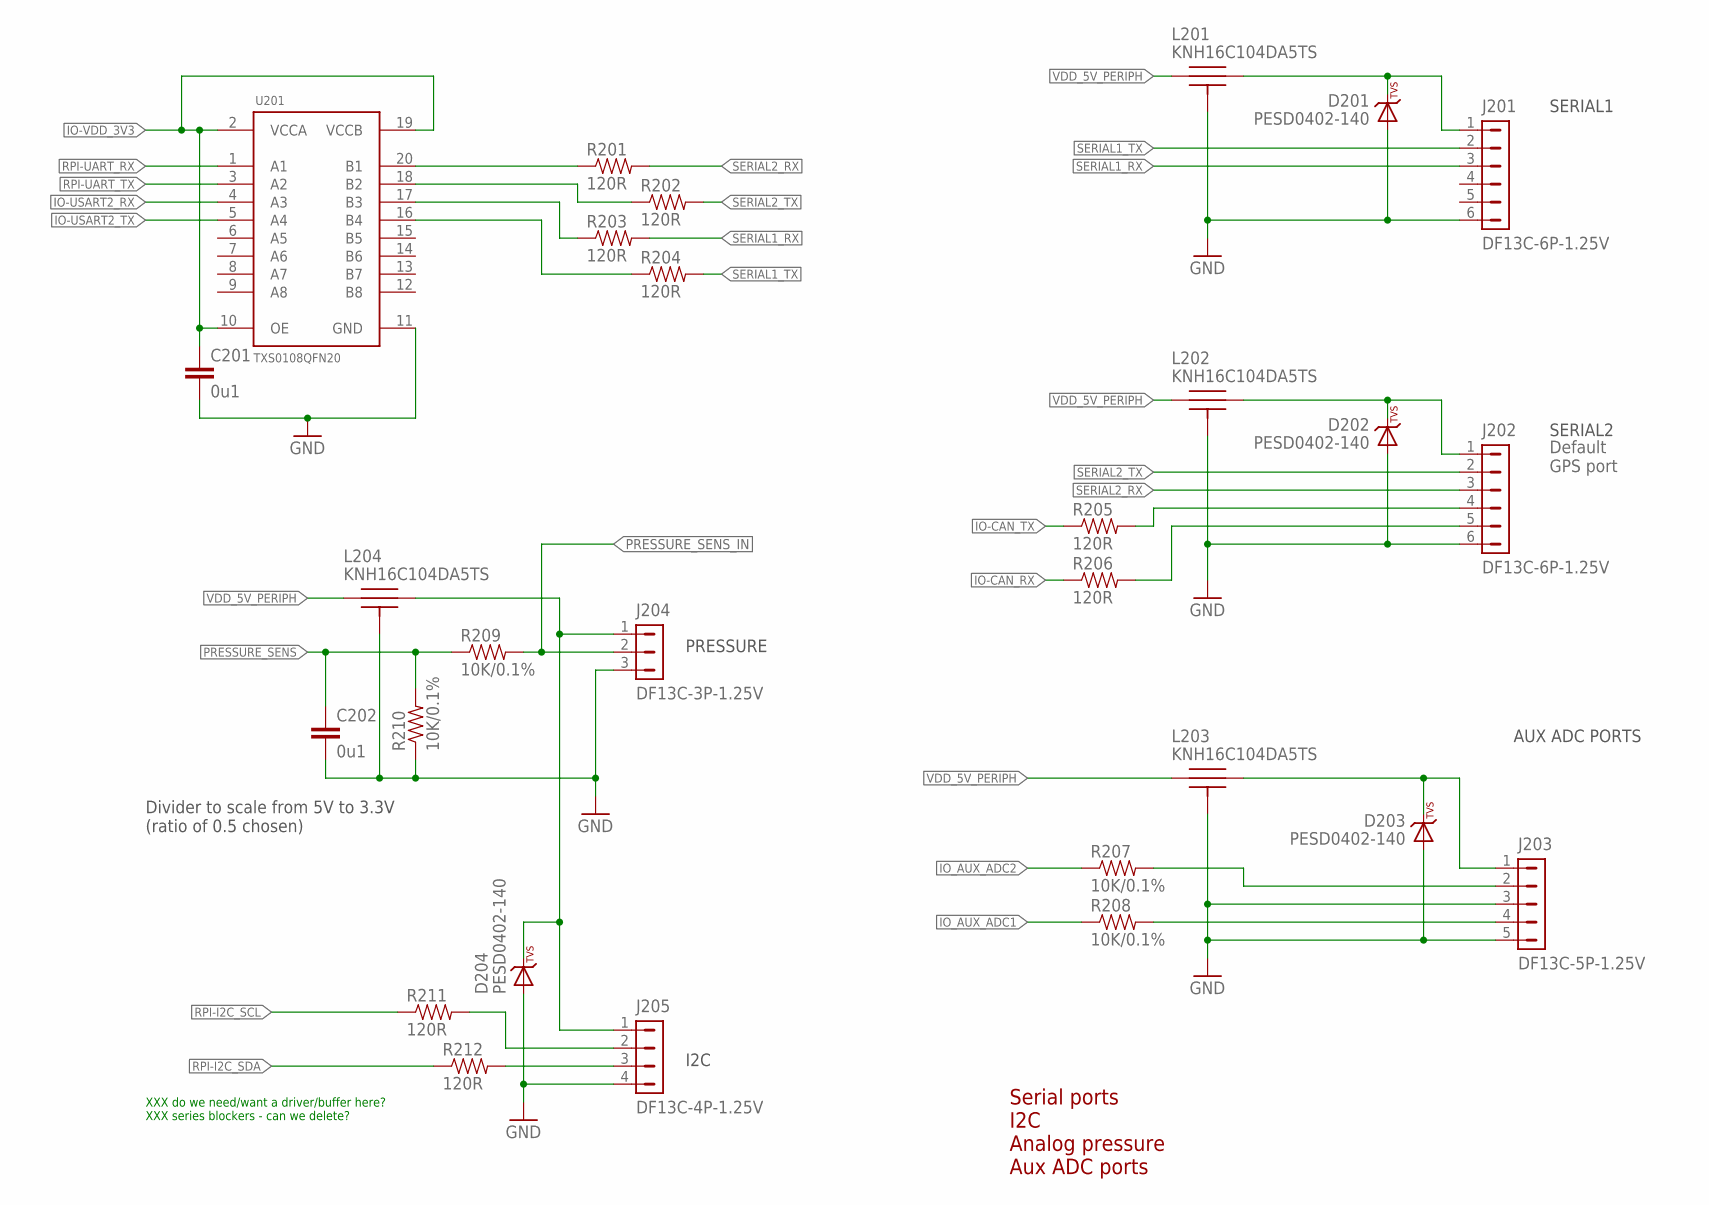
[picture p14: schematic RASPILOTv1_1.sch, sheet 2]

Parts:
C201, C202: 0u1; 0402-CAP; PARTNO CC0402ZRY5V7BB104
D201, D202, D203, D204: PESD0402-140; 0402-TVS; PARTNO PESD0402-140
J201, J202: DF13C-6P-1.25V; PARTNO DF13C-6P-1.25V(20)
J203: DF13C-5P-1.25V; PARTNO DF13C-5P-1.25V(20)
J204: DF13C-3P-1.25V; PARTNO DF13C-3P-1.25V(20)
J205: DF13C-4P-1.25V; PARTNO DF13C-4P-1.25V(20)
L201, L202, L203, L204: KNH16C104DA5TS; KYOCERA-KNH16-DA; PARTNO KNH16C104DA5TS
R201, R202, R203, R204, R205, R206, R211, R212: 120R; 0402-RES; PARTNO RC0402FR-07120RL
R207, R208, R209, R210: 10K/0.1%; 0402-RES; PARTNO ERA-2AEB103X
U201: TXS0108QFN20; QFN20-RGY; PARTNO TXS0108ERGYR

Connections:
FMU_AUX_ADC1_PROT1: J203.4, R208.P$2 (2)
FMU_AUX_ADC2_PROT1: J203.2, R207.P$2 (2)
GND: C201.P$2 (2), C202.P$2 (2), D201.A, D202.A, D203.A, D204.A, J201.6, J202.6, J203.3, J203.5, J204.3, J205.4, L201.P$3, L201.P$4, L201.P$5, L202.P$3, L202.P$4, L202.P$5, L203.P$3, L203.P$4, L203.P$5, L204.P$3, L204.P$4, L204.P$5, R210.P$1 (1), U201.11 (GND); also elsewhere on the board
IO-CAN_RX: R206.P$1 (1); also elsewhere on the board
IO-CAN_TX: R205.P$1 (1); also elsewhere on the board
IO-USART2_RX: U201.4 (A3); also elsewhere on the board
IO-USART2_TX: U201.5 (A4); also elsewhere on the board
IO-VDD_3V3: C201.P$1 (1), U201.2 (VCCA), U201.10 (OE), U201.19 (VCCB); also elsewhere on the board
IO_AUX_ADC1: R208.P$1 (1); also elsewhere on the board
IO_AUX_ADC2: R207.P$1 (1); also elsewhere on the board
unnamed: D203.C, J203.1, L203.P$2
unnamed: D201.C, J201.1, L201.P$2
unnamed: J205.2, R211.P$2 (2)
unnamed: J205.3, R212.P$2 (2)
unnamed: D204.C, J204.1, J205.1, L204.P$2
unnamed: J202.4, R205.P$2 (2)
unnamed: J202.5, R206.P$2 (2)
unnamed: R201.P$1 (1), U201.20 (B1)
unnamed: R202.P$1 (1), U201.18 (B2)
unnamed: R203.P$1 (1), U201.17 (B3)
unnamed: R204.P$1 (1), U201.16 (B4)
unnamed: D202.C, J202.1, L202.P$2
PRESSURE_SENS: C202.P$1 (1), R209.P$1 (1), R210.P$2 (2); also elsewhere on the board
PRESSURE_SENS_IN: J204.2, R209.P$2 (2); also elsewhere on the board
RPI-I2C_SCL: R211.P$1 (1); also elsewhere on the board
RPI-I2C_SDA: R212.P$1 (1); also elsewhere on the board
RPI-UART_RX: U201.1 (A1); also elsewhere on the board
RPI-UART_TX: U201.3 (A2); also elsewhere on the board
SERIAL1_RX: J201.3, R203.P$2 (2); also elsewhere on the board
SERIAL1_TX: J201.2, R204.P$2 (2); also elsewhere on the board
SERIAL2_RX: J202.3, R201.P$2 (2); also elsewhere on the board
SERIAL2_TX: J202.2, R202.P$2 (2); also elsewhere on the board
VDD_5V_PERIPH: L201.P$1, L202.P$1, L203.P$1, L204.P$1; also elsewhere on the board

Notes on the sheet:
Serial ports I2C Analog pressure Aux ADC ports
SERIAL1
SERIAL2
Default GPS port
AUX ADC PORTS
PRESSURE
XXX do we need/want a driver/buffer here? XXX series blockers - can we delete?
I2C
Divider to scale from 5V to 3.3V (ratio of 0.5 chosen)

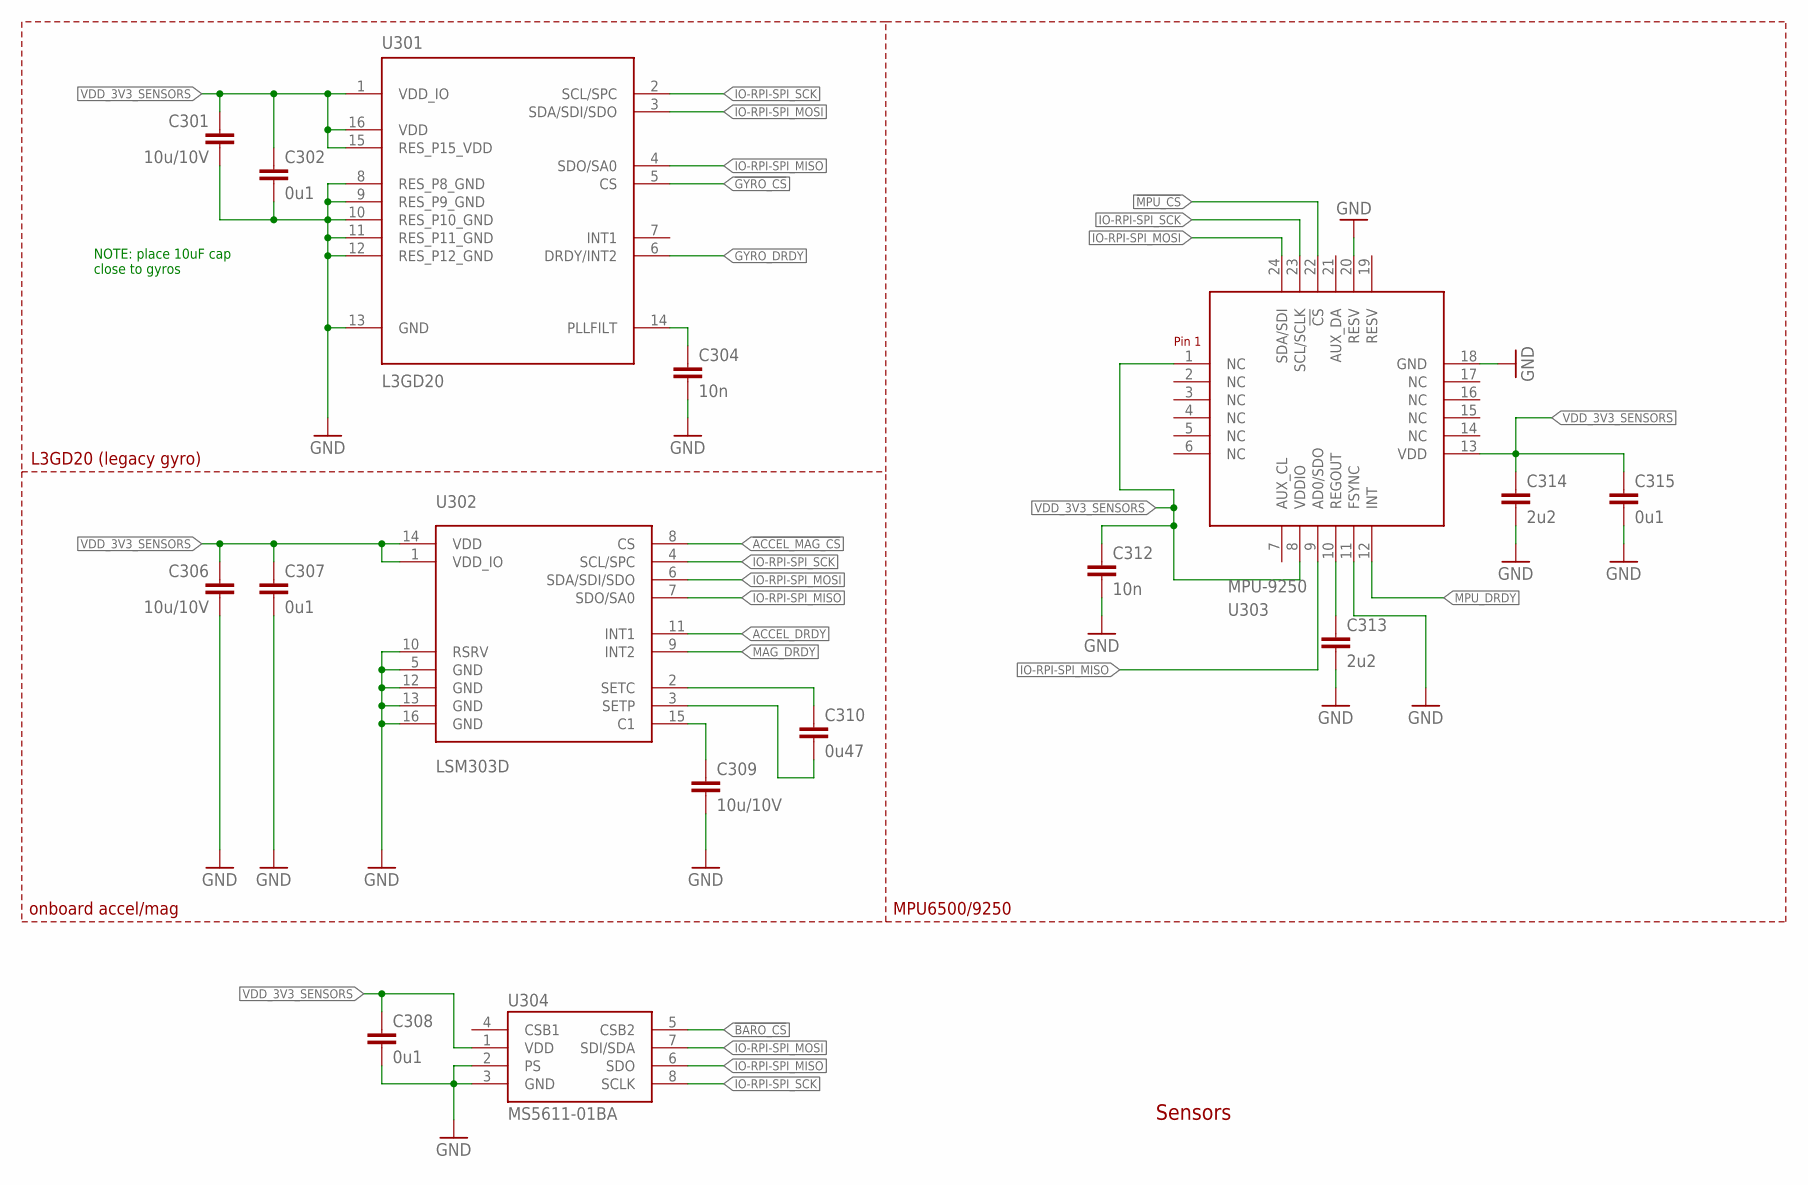
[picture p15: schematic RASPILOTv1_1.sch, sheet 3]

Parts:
C301, C306, C309: 10u/10V; 0805-CAP; PARTNO CC0805ZKY5V6BB106
C302, C307, C308, C315: 0u1; 0402-CAP; PARTNO CC0402ZRY5V7BB104
C304: 10n; 0402-CAP; PARTNO CC0402KRX7R7BB103
C310: 0u47; 0402-CAP; PARTNO C1005X5R1C474K050BC
C312: 10n; 0603-CAP; PARTNO C0603C103J5RAC7411
C313: 2u2; 0603-CAP; PARTNO C1608X6S1C225K080AC
C314: 2u2; 0603-CAP
U301: L3GD20; L3G4200DH-MAN; PARTNO L3GD20
U302: LSM303D; LGA-16L; PARTNO LSM303D
U303: MPU-9250; MPU-6500; PARTNO MPU-9250
U304: MS5611-01BA; PARTNO MS5611-01BA

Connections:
!ACCEL_MAG_CS: U302.8 (CS); also elsewhere on the board
!BARO_CS: U304.5 (CSB2); also elsewhere on the board
!GYRO_CS: U301.5 (CS); also elsewhere on the board
!MPU_CS: U303.22 (!CS); also elsewhere on the board
ACCEL_DRDY: U302.11 (INT1); also elsewhere on the board
GND: C301.P$2 (2), C302.P$2 (2), C304.P$2 (2), C306.P$2 (2), C307.P$2 (2), C308.P$2 (2), C309.P$2 (2), C312.P$2 (2), C313.P$2 (2), C314.P$2 (2), C315.P$2 (2), U301.8 (RES_P8_GND), U301.9 (RES_P9_GND), U301.10 (RES_P10_GND), U301.11 (RES_P11_GND), U301.12 (RES_P12_GND), U301.13 (GND), U302.5 (GND), U302.10 (RSRV), U302.12 (GND), U302.13 (GND), U302.16 (GND), U303.11 (FSYNC), U303.18 (GND), U303.20 (RESV), U304.2 (PS), U304.3 (GND); also elsewhere on the board
GYRO_DRDY: U301.6 (DRDY/INT2); also elsewhere on the board
IO-RPI-SPI_MISO: U301.4 (SDO/SA0), U302.7 (SDO/SA0), U303.9 (AD0/SDO), U304.6 (SDO); also elsewhere on the board
IO-RPI-SPI_MOSI: U301.3 (SDA/SDI/SDO), U302.6 (SDA/SDI/SDO), U303.24 (SDA/SDI), U304.7 (SDI/SDA); also elsewhere on the board
IO-RPI-SPI_SCK: U301.2 (SCL/SPC), U302.4 (SCL/SPC), U303.23 (SCL/SCLK), U304.8 (SCLK); also elsewhere on the board
MAG_DRDY: U302.9 (INT2); also elsewhere on the board
MPU_DRDY: U303.12 (INT); also elsewhere on the board
unnamed: C309.P$1 (1), U302.15 (C1)
unnamed: C310.P$1 (1), U302.2 (SETC)
unnamed: C313.P$1 (1), U303.10 (REGOUT)
unnamed: C310.P$2 (2), U302.3 (SETP)
unnamed: C304.P$1 (1), U301.14 (PLLFILT)
VDD_3V3_SENSORS: C301.P$1 (1), C302.P$1 (1), C306.P$1 (1), C307.P$1 (1), C308.P$1 (1), C312.P$1 (1), C314.P$1 (1), C315.P$1 (1), U301.1 (VDD_IO), U301.15 (RES_P15_VDD), U301.16 (VDD), U302.1 (VDD_IO), U302.14 (VDD), U303.1 (NC), U303.8 (VDDIO), U303.13 (VDD), U304.1 (VDD); also elsewhere on the board

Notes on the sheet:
Sensors
NOTE: place 10uF cap close to gyros
L3GD20 (legacy gyro)
onboard accel/mag
MPU6500/9250

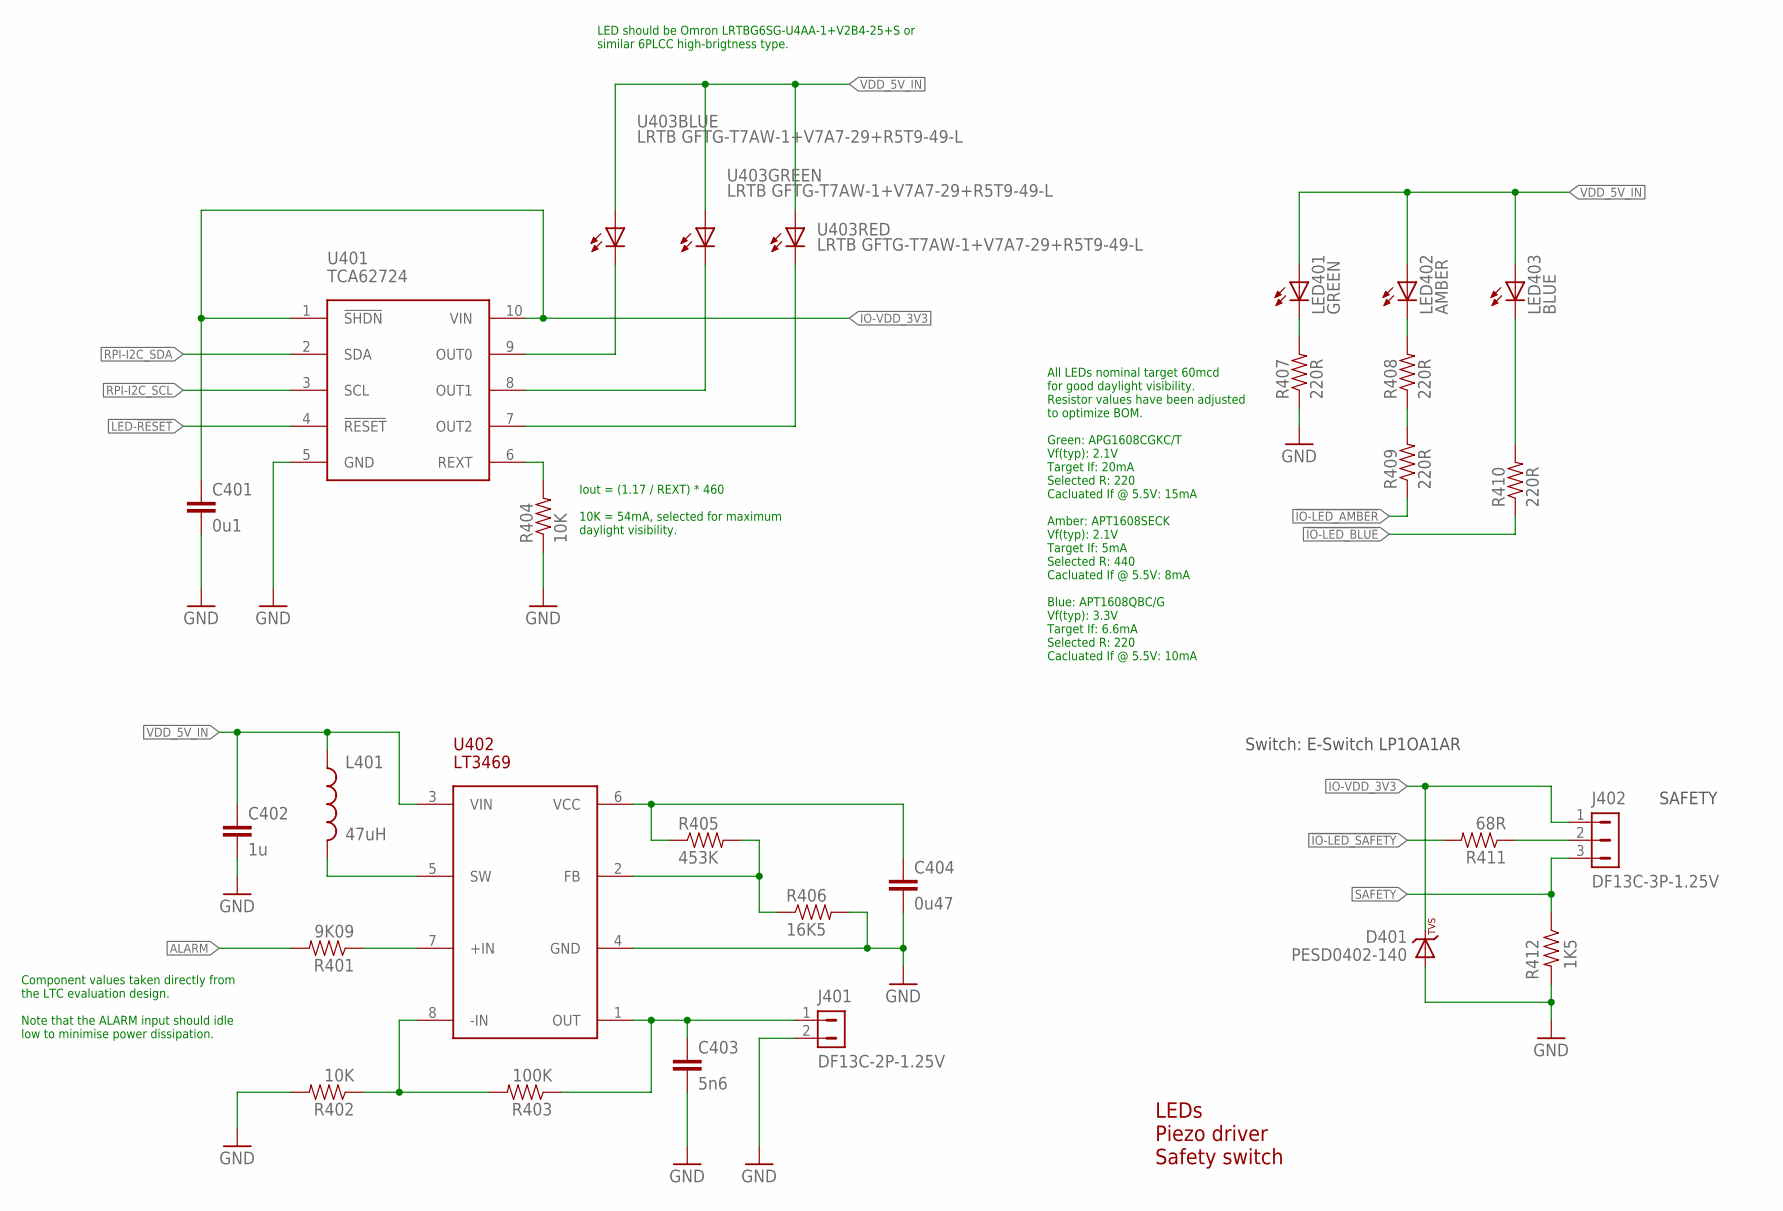
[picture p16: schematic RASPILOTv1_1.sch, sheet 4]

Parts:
C401: 0u1; 0402-CAP; PARTNO CC0402ZRY5V7BB104
C402: 1u; 0603-CAP; PARTNO CC0603ZRY5V7BB105
C403: 5n6; 0402-CAP; PARTNO C0402C562K5RACTU
C404: 0u47; 0402-CAP; PARTNO C1005X5R1C474K050BC
D401: PESD0402-140; 0402-TVS; PARTNO PESD0402-140
J401: DF13C-2P-1.25V; PARTNO DF13C-2P-1.25V(20)
J402: DF13C-3P-1.25V; PARTNO DF13C-3P-1.25V(20)
L401: 47uH; 0805-IND; PARTNO MLZ2012M470W
LED401: GREEN; 0603-LED; PARTNO APTD1608CGCK
LED402: AMBER; 0603-LED; PARTNO APTD1608SECK
LED403: BLUE; 0603-LED; PARTNO APTD1608QBC/D
R401: 9K09; 0402-RES; PARTNO RMCF0402FT9K09
R402, R404: 10K; 0402-RES; PARTNO RC0402FR-0710KL
R403: 100K; 0402-RES; PARTNO RC0402FR-07100KL
R405: 453K; 0402-RES; PARTNO RMCF0402FT453K
R406: 16K5; 0402-RES; PARTNO RMCF0402FT16K5
R407, R408, R409, R410: 220R; 0402-RES; PARTNO RC0402FR-07220RL
R411: 68R; 0402-RES; PARTNO ERJ-2GEJ680X
R412: 1K5; 0402-RES; PARTNO RC0402FR-071K5L
U401: TCA62724FMG; SON10; PARTNO TCA62724FMG
U402: LT3469; SOT23-8; PARTNO LT3469ETS8
U403: LRTB GFTG-T7AW-1+V7A7-29+R5T9-49-L; 6-PLCC; PARTNO LRTB GFTG-T7AW-1+V7A7-29+R5T9-49-L

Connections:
!IO-LED_AMBER: R409.P$1 (1); also elsewhere on the board
!IO-LED_BLUE: R410.P$1 (1); also elsewhere on the board
!IO-LED_SAFETY: R411.P$2 (2); also elsewhere on the board
ALARM: R401.P$2 (2); also elsewhere on the board
GND: C401.P$2 (2), C402.P$2 (2), C403.P$2 (2), C404.P$2 (2), D401.A, J401.2, R402.P$2 (2), R404.P$1 (1), R406.P$2 (2), R407.P$1 (1), R412.P$2 (2), U401.5 (GND), U402.4 (GND); also elsewhere on the board
IO-VDD_3V3: C401.P$1 (1), D401.C, J402.1, U401.1 (!SHDN), U401.10 (VIN); also elsewhere on the board
LED-!RESET: U401.4 (!RESET); also elsewhere on the board
unnamed: LED403.C, R410.P$2 (2)
unnamed: R405.P$2 (2), R406.P$1 (1), U402.2 (FB)
unnamed: R402.P$1 (1), R403.P$2 (2), U402.8 (-IN)
unnamed: C403.P$1 (1), J401.1, R403.P$1 (1), U402.1 (OUT)
unnamed: R401.P$1 (1), U402.7 (+IN)
unnamed: LED401.C, R407.P$2 (2)
unnamed: L401.P$2 (2), U402.5 (SW)
unnamed: C404.P$1 (1), R405.P$1 (1), U402.6 (VCC)
unnamed: R408.P$1 (1), R409.P$2 (2)
unnamed: LED402.C, R408.P$2 (2)
unnamed: J402.2, R411.P$1 (1)
unnamed: R404.P$2 (2), U401.6 (REXT)
RGB_LED_3: U401.9 (OUT0), U403.C1 (C)
RGB_LED_4: U401.8 (OUT1), U403.C2 (C)
RGB_LED_14: U401.7 (OUT2), U403.C3 (C)
RPI-I2C_SCL: U401.3 (SCL); also elsewhere on the board
RPI-I2C_SDA: U401.2 (SDA); also elsewhere on the board
SAFETY: J402.3, R412.P$1 (1); also elsewhere on the board
VDD_5V_IN: C402.P$1 (1), L401.P$1 (1), LED401.A, LED402.A, LED403.A, U402.3 (VIN), U403.A1 (A), U403.A2 (A), U403.A3 (A); also elsewhere on the board

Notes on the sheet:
LEDs Piezo driver Safety switch
Switch: E-Switch LP1OA1AR
SAFETY
LED should be Omron LRTBG6SG-U4AA-1+V2B4-25+S or similar 6PLCC high-brigtness type.
Iout = (1.17 / REXT) * 460 10K = 54mA, selected for maximum daylight visibility.
All LEDs nominal target 60mcd for good daylight visibility. Resistor values have been adjusted to optimize BOM. Green: APG1608CGKC/T Vf(typ): 2.1V Target If: 20mA Selected R: 220 Cacluated If @ 5.5V: 15mA Amber: APT1608SECK Vf(typ): 2.1V Target If: 5mA Selected R: 440 Cacluated If @ 5.5V: 8mA Blue: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
Component values taken directly from the LTC evaluation design. Note that the ALARM input should idle low to minimise power dissipation.

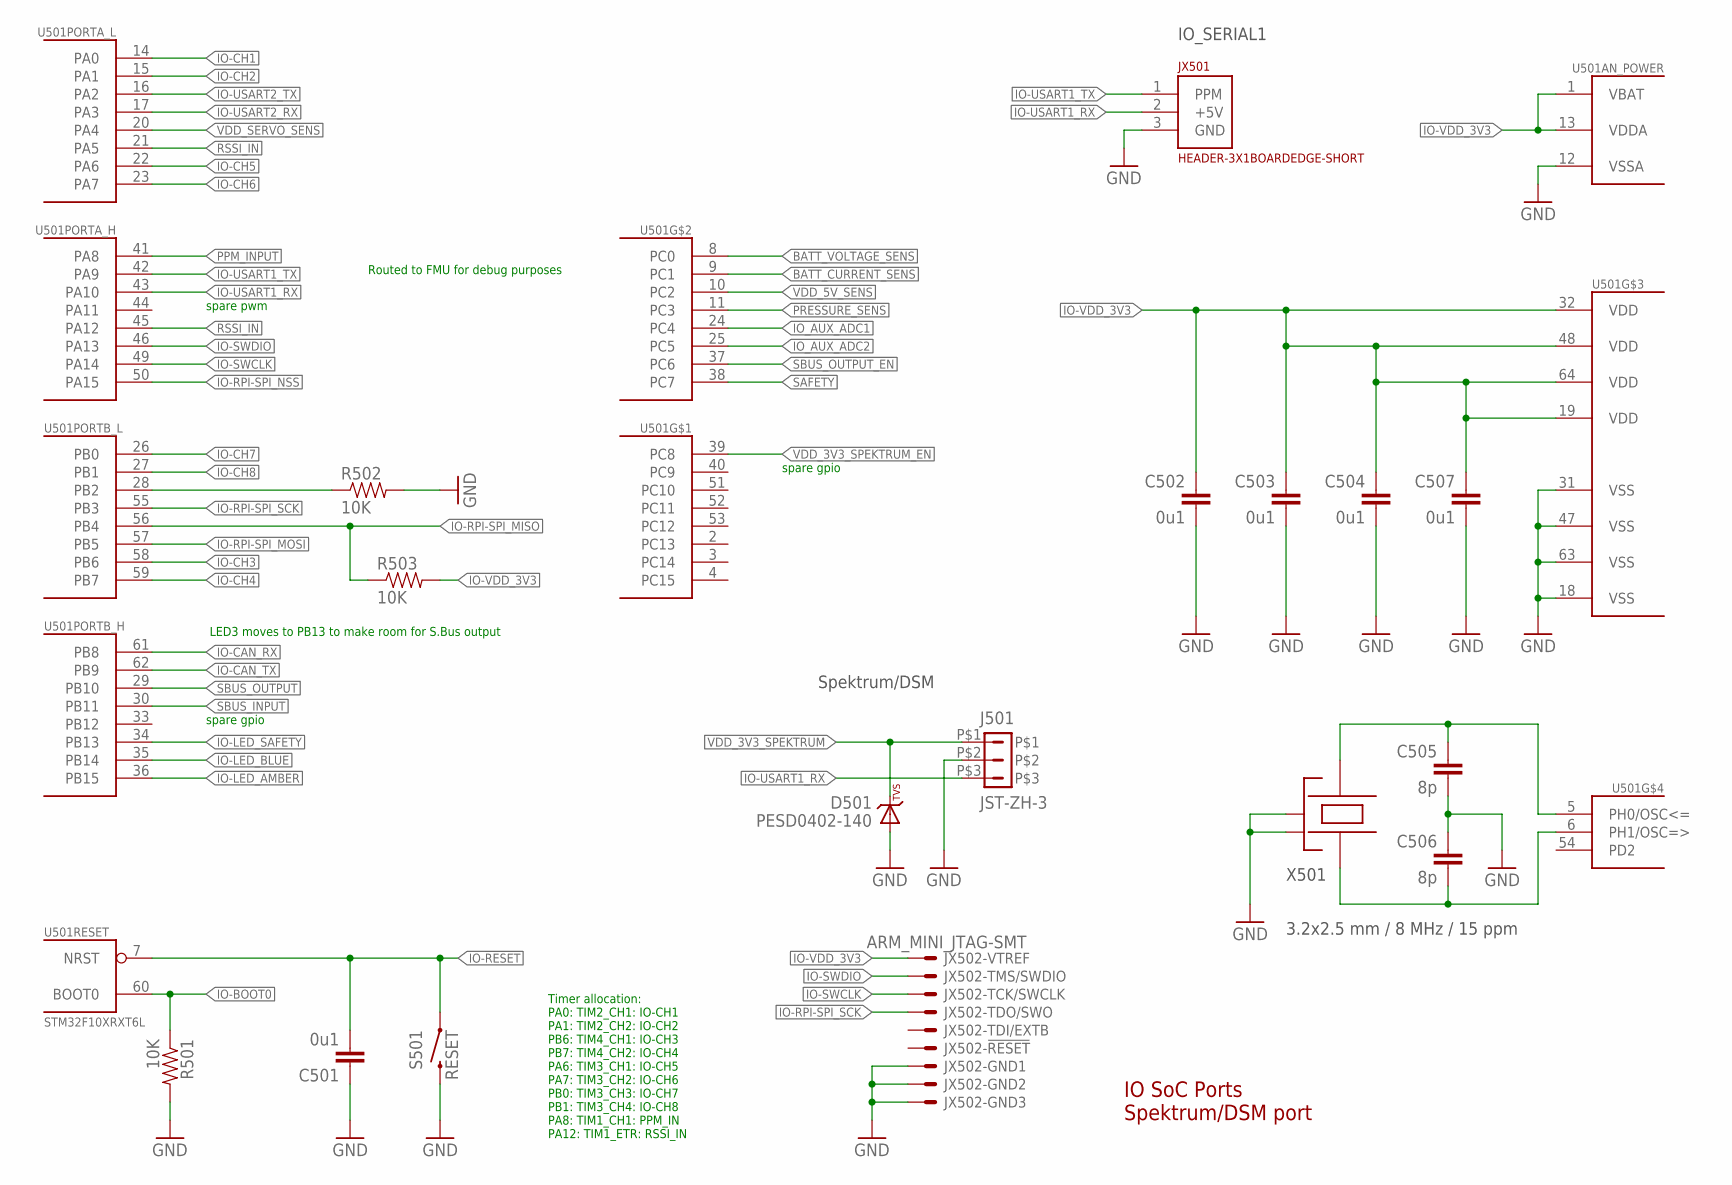
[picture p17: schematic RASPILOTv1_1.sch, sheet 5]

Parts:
C501, C502, C503, C504, C507: 0u1; 0402-CAP; PARTNO CC0402ZRY5V7BB104
C505, C506: 8p; 0402-CAP; PARTNO C1005C0G1H080C
D501: PESD0402-140; 0402-TVS; PARTNO PESD0402-140
J501: JST-ZH-3; JST-ZH-SMT-VERTICAL; PARTNO B3B-ZR-SM4-TF (LF)(SN)(P)
JX501: HEADER-3X1BOARDEDGE-SHORT; HEADER_3X01_SMD_H_BOARD_EDGE_SHORT
JX502: ARM_MINI_JTAG-SMT; FTSH-105-01-XXX-DV-K; PARTNO M50-3900542
R501, R502, R503: 10K; 0402-RES; PARTNO RC0402FR-0710KL
S501: RESET; EVQP7J01K; PARTNO EVQ-P7J01P
U501: STM32F10XRXT6L; TQFP64
X501: 3.2x2.5 mm / 8 MHz / 15 ppm; OSCILLATOR-3.2X2.5; PARTNO NX3225SA-24.000000MHZ

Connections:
!IO-LED_AMBER: U501.36 (PB15); also elsewhere on the board
!IO-LED_BLUE: U501.35 (PB14); also elsewhere on the board
!IO-LED_SAFETY: U501.34 (PB13); also elsewhere on the board
!SBUS_OUTPUT_EN: U501.37 (PC6); also elsewhere on the board
BATT_CURRENT_SENS: U501.9 (PC1); also elsewhere on the board
BATT_VOLTAGE_SENS: U501.8 (PC0); also elsewhere on the board
GND: C501.P$1 (1), C502.P$2 (2), C503.P$2 (2), C504.P$2 (2), C505.P$2 (2), C506.P$1 (1), C507.P$2 (2), D501.A, J501.P$2, JX501.3 (GND), JX502.3, JX502.5, JX502.9, R501.P$2 (2), R502.P$2 (2), S501.B3 (2), U501.12 (VSSA), U501.18 (VSS), U501.31 (VSS), U501.47 (VSS), U501.63 (VSS), X501.2 (NC_2), X501.4 (NC_4); also elsewhere on the board
IO-!RESET: C501.P$2 (2), S501.A1 (1), U501.7 (NRST); also elsewhere on the board
IO-BOOT0: R501.P$1 (1), U501.60 (BOOT0); also elsewhere on the board
IO-BOOT1: R502.P$1 (1), U501.28 (PB2)
IO-CAN_RX: U501.61 (PB8); also elsewhere on the board
IO-CAN_TX: U501.62 (PB9); also elsewhere on the board
IO-CH1: U501.14 (PA0); also elsewhere on the board
IO-CH2: U501.15 (PA1); also elsewhere on the board
IO-CH3: U501.58 (PB6); also elsewhere on the board
IO-CH4: U501.59 (PB7); also elsewhere on the board
IO-CH5: U501.22 (PA6); also elsewhere on the board
IO-CH6: U501.23 (PA7); also elsewhere on the board
IO-CH7: U501.26 (PB0); also elsewhere on the board
IO-CH8: U501.27 (PB1); also elsewhere on the board
IO-RPI-SPI_MISO: R503.P$1 (1), U501.56 (PB4); also elsewhere on the board
IO-RPI-SPI_MOSI: U501.57 (PB5); also elsewhere on the board
IO-RPI-SPI_NSS: U501.50 (PA15); also elsewhere on the board
IO-RPI-SPI_SCK: JX502.6, U501.55 (PB3); also elsewhere on the board
IO-SWCLK: JX502.4, U501.49 (PA14)
IO-SWDIO: JX502.2, U501.46 (PA13)
IO-USART1_RX: J501.P$3, JX501.2 (+5V), U501.43 (PA10)
IO-USART1_TX: JX501.1 (PPM), U501.42 (PA9)
IO-USART2_RX: U501.17 (PA3); also elsewhere on the board
IO-USART2_TX: U501.16 (PA2); also elsewhere on the board
IO-VDD_3V3: C502.P$1 (1), C503.P$1 (1), C504.P$1 (1), C507.P$1 (1), JX502.1, R503.P$2 (2), U501.1 (VBAT), U501.13 (VDDA), U501.19 (VDD), U501.32 (VDD), U501.48 (VDD), U501.64 (VDD); also elsewhere on the board
IO_AUX_ADC1: U501.24 (PC4); also elsewhere on the board
IO_AUX_ADC2: U501.25 (PC5); also elsewhere on the board
unnamed: C506.P$2 (2), U501.6 (PH1/OSC=>), X501.1
unnamed: C505.P$1 (1), U501.5 (PH0/OSC<=), X501.3
PPM_INPUT: U501.41 (PA8); also elsewhere on the board
PRESSURE_SENS: U501.11 (PC3); also elsewhere on the board
RSSI_IN: U501.21 (PA5), U501.45 (PA12); also elsewhere on the board
SAFETY: U501.38 (PC7); also elsewhere on the board
SBUS_INPUT: U501.30 (PB11); also elsewhere on the board
SBUS_OUTPUT: U501.29 (PB10); also elsewhere on the board
VDD_3V3_SPEKTRUM: D501.C, J501.P$1; also elsewhere on the board
VDD_3V3_SPEKTRUM_EN: U501.39 (PC8); also elsewhere on the board
VDD_5V_SENS: U501.10 (PC2); also elsewhere on the board
VDD_SERVO_SENS: U501.20 (PA4); also elsewhere on the board

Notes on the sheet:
IO SoC Ports Spektrum/DSM port
LED3 moves to PB13 to make room for S.Bus output
Routed to FMU for debug purposes
IO_SERIAL1
Spektrum/DSM
Timer allocation: PA0: TIM2_CH1: IO-CH1 PA1: TIM2_CH2: IO-CH2 PB6: TIM4_CH1: IO-CH3 PB7: TIM4_CH2: IO-CH4 PA6: TIM3_CH1: IO-CH5 PA7: TIM3_CH2: IO-CH6 PB0: TIM3_CH3: IO-CH7 PB1: TIM3_CH4: IO-CH8 PA8: TIM1_CH1: PPM_IN PA12: TIM1_ETR: RSSI_IN
spare pwm
spare gpio

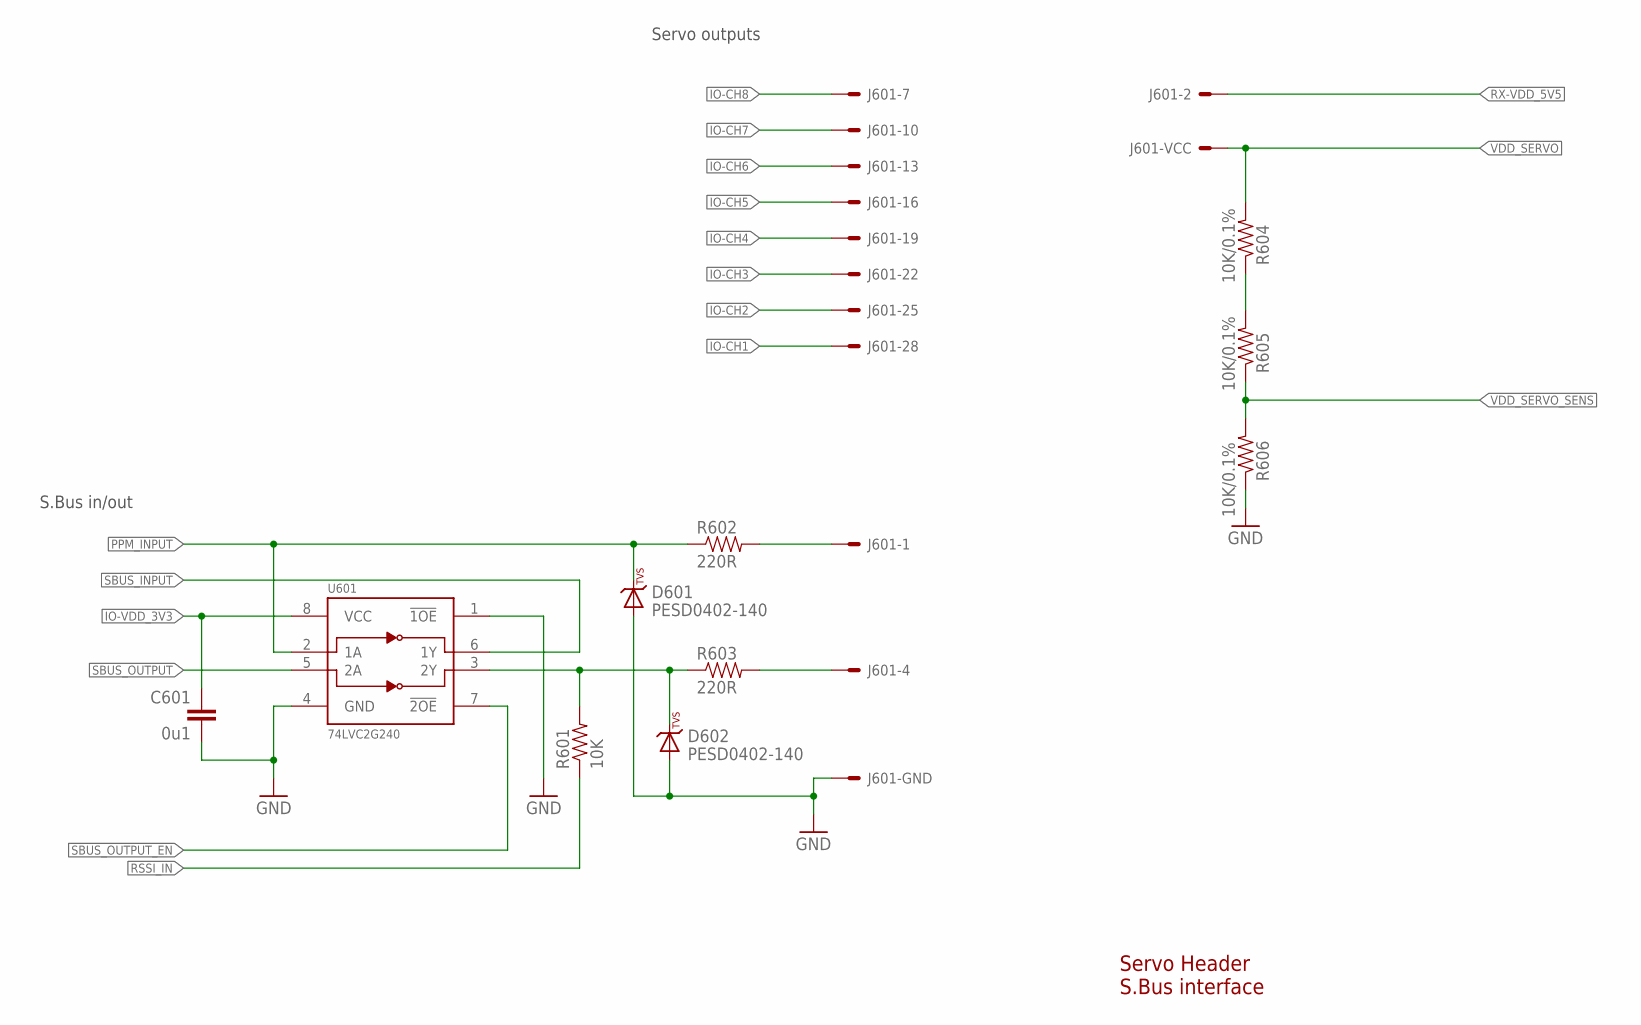
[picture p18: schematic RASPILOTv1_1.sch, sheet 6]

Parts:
C601: 0u1; 0402-CAP; PARTNO CC0402ZRY5V7BB104
D601, D602: PESD0402-140; 0402-TVS; PARTNO PESD0402-140
J601: HEADER-3X10; 3X10RA
R601: 10K; 0402-RES; PARTNO RC0402FR-0710KL
R602, R603: 220R; 0402-RES; PARTNO RC0402FR-07220RL
R604, R605, R606: 10K/0.1%; 0402-RES; PARTNO ERA-2AEB103X
U601: 74LVC2G240; TSSOP8_SOT505-2; PARTNO 74LVC2G240DP,125

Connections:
!SBUS_OUTPUT_EN: U601.7 (!2OE); also elsewhere on the board
GND: C601.P$2 (2), D601.A, D602.A, J601.3, J601.6, J601.9, J601.12, J601.15, J601.18, J601.21, J601.24, J601.27, J601.30, R606.P$1 (1), U601.1 (!1OE), U601.4 (GND); also elsewhere on the board
IO-CH1: J601.28; also elsewhere on the board
IO-CH2: J601.25; also elsewhere on the board
IO-CH3: J601.22; also elsewhere on the board
IO-CH4: J601.19; also elsewhere on the board
IO-CH5: J601.16; also elsewhere on the board
IO-CH6: J601.13; also elsewhere on the board
IO-CH7: J601.10; also elsewhere on the board
IO-CH8: J601.7; also elsewhere on the board
IO-VDD_3V3: C601.P$1 (1), U601.8 (VCC); also elsewhere on the board
unnamed: R604.P$1 (1), R605.P$2 (2)
unnamed: D602.C, R601.P$2 (2), R603.P$1 (1), U601.3 (2Y)
unnamed: J601.4, R603.P$2 (2)
PPM-SBUS-PROT: J601.1, R602.P$2 (2)
PPM_INPUT: D601.C, R602.P$1 (1), U601.2 (1A); also elsewhere on the board
RSSI_IN: R601.P$1 (1); also elsewhere on the board
RX-VDD_5V5: J601.2; also elsewhere on the board
SBUS_INPUT: U601.6 (1Y); also elsewhere on the board
SBUS_OUTPUT: U601.5 (2A); also elsewhere on the board
VDD_SERVO: J601.5, J601.8, J601.11, J601.14, J601.17, J601.20, J601.23, J601.26, J601.29, R604.P$2 (2); also elsewhere on the board
VDD_SERVO_SENS: R605.P$1 (1), R606.P$2 (2); also elsewhere on the board

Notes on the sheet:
Servo Header S.Bus interface
S.Bus in/out
Servo outputs

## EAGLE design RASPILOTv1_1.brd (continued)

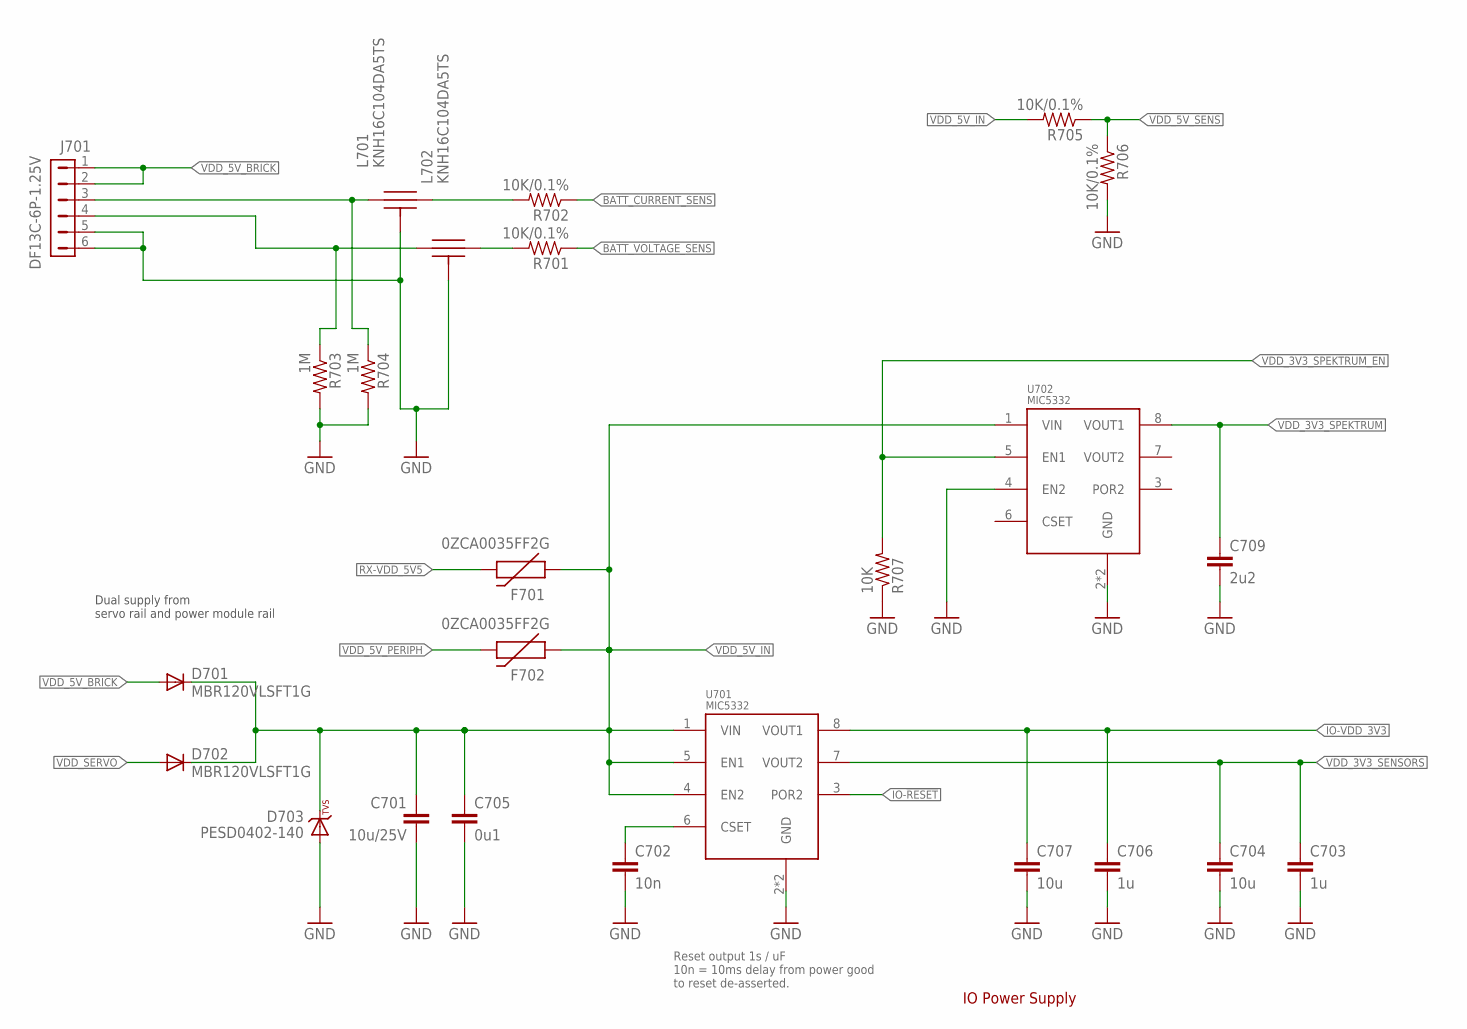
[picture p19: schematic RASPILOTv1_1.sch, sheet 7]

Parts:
C701: 10u/25V; 0805-CAP; PARTNO CL21A106KAYNNNE
C702: 10n; 0402-CAP; PARTNO CC0402KRX7R7BB103
C703, C706: 1u; 0603-CAP; PARTNO CC0603ZRY5V7BB105
C704, C707: 10u; 0603-CAP; PARTNO C1608X5R1A106K080AC
C705: 0u1; 0402-CAP; PARTNO CC0402ZRY5V7BB104
C709: 2u2; 0402-CAP; PARTNO C1005X6S1C225K050BC
D701, D702: MBR120VLSFT1G; SOD-123-DIO
D703: PESD0402-140; 0402-TVS; PARTNO PESD0402-140
F701, F702: 0ZCA0035FF2G; PTC-1206; PARTNO 0ZCA0035FF2G
J701: DF13C-6P-1.25V; PARTNO DF13C-6P-1.25V(20)
L701, L702: KNH16C104DA5TS; KYOCERA-KNH16-DA; PARTNO KNH16C104DA5TS
R701, R702, R705, R706: 10K/0.1%; 0402-RES; PARTNO ERA-2AEB103X
R703, R704: 1M; 0402-RES; PARTNO RC0402FR-071ML
R707: 10K; 0402-RES; PARTNO RC0402FR-0710KL
U701, U702: MIC5332; MLF-8-EPAD; PARTNO MIC5332-SSYMT

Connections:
BATT_CURRENT_SENS: R702.P$1 (1); also elsewhere on the board
BATT_CURRENT_SENS_PROT1: J701.3, L701.P$1, R704.P$1 (1)
BATT_VOLTAGE_SENS: R701.P$1 (1); also elsewhere on the board
BATT_VOLTAGE_SENS_PROT1: J701.4, L702.P$1, R703.P$1 (1)
GND: C701.P$2 (2), C702.P$2 (2), C703.P$2 (2), C704.P$2 (2), C705.P$2 (2), C706.P$2 (2), C707.P$2 (2), C709.P$2 (2), D703.A, J701.5, J701.6, L701.P$3, L701.P$4, L701.P$5, L702.P$3, L702.P$4, L702.P$5, R703.P$2 (2), R704.P$2 (2), R706.P$2 (2), R707.P$1 (1), U701.2 (GND), U701.GND, U702.2 (GND), U702.4 (EN2), U702.GND; also elsewhere on the board
IO-!RESET: U701.3 (POR2); also elsewhere on the board
IO-VDD_3V3: C706.P$1 (1), C707.P$1 (1), U701.8 (VOUT1); also elsewhere on the board
unnamed: L702.P$2, R701.P$2 (2)
unnamed: L701.P$2, R702.P$2 (2)
unnamed: C702.P$1 (1), U701.6 (CSET)
RX-VDD_5V5: F701.2; also elsewhere on the board
VDD_3V3_SENSORS: C703.P$1 (1), C704.P$1 (1), U701.7 (VOUT2); also elsewhere on the board
VDD_3V3_SPEKTRUM: C709.P$1 (1), U702.8 (VOUT1); also elsewhere on the board
VDD_3V3_SPEKTRUM_EN: R707.P$2 (2), U702.5 (EN1); also elsewhere on the board
VDD_5V_BRICK: D701.A, J701.1, J701.2; also elsewhere on the board
VDD_5V_IN: C701.P$1 (1), C705.P$1 (1), D701.C, D702.C, D703.C, F701.1, F702.1, R705.P$2 (2), U701.1 (VIN), U701.4 (EN2), U701.5 (EN1), U702.1 (VIN); also elsewhere on the board
VDD_5V_PERIPH: F702.2; also elsewhere on the board
VDD_5V_SENS: R705.P$1 (1), R706.P$1 (1); also elsewhere on the board
VDD_SERVO: D702.A; also elsewhere on the board

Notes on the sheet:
Dual supply from servo rail and power module rail
IO Power Supply
Reset output 1s / uF 10n = 10ms delay from power good to reset de-asserted.

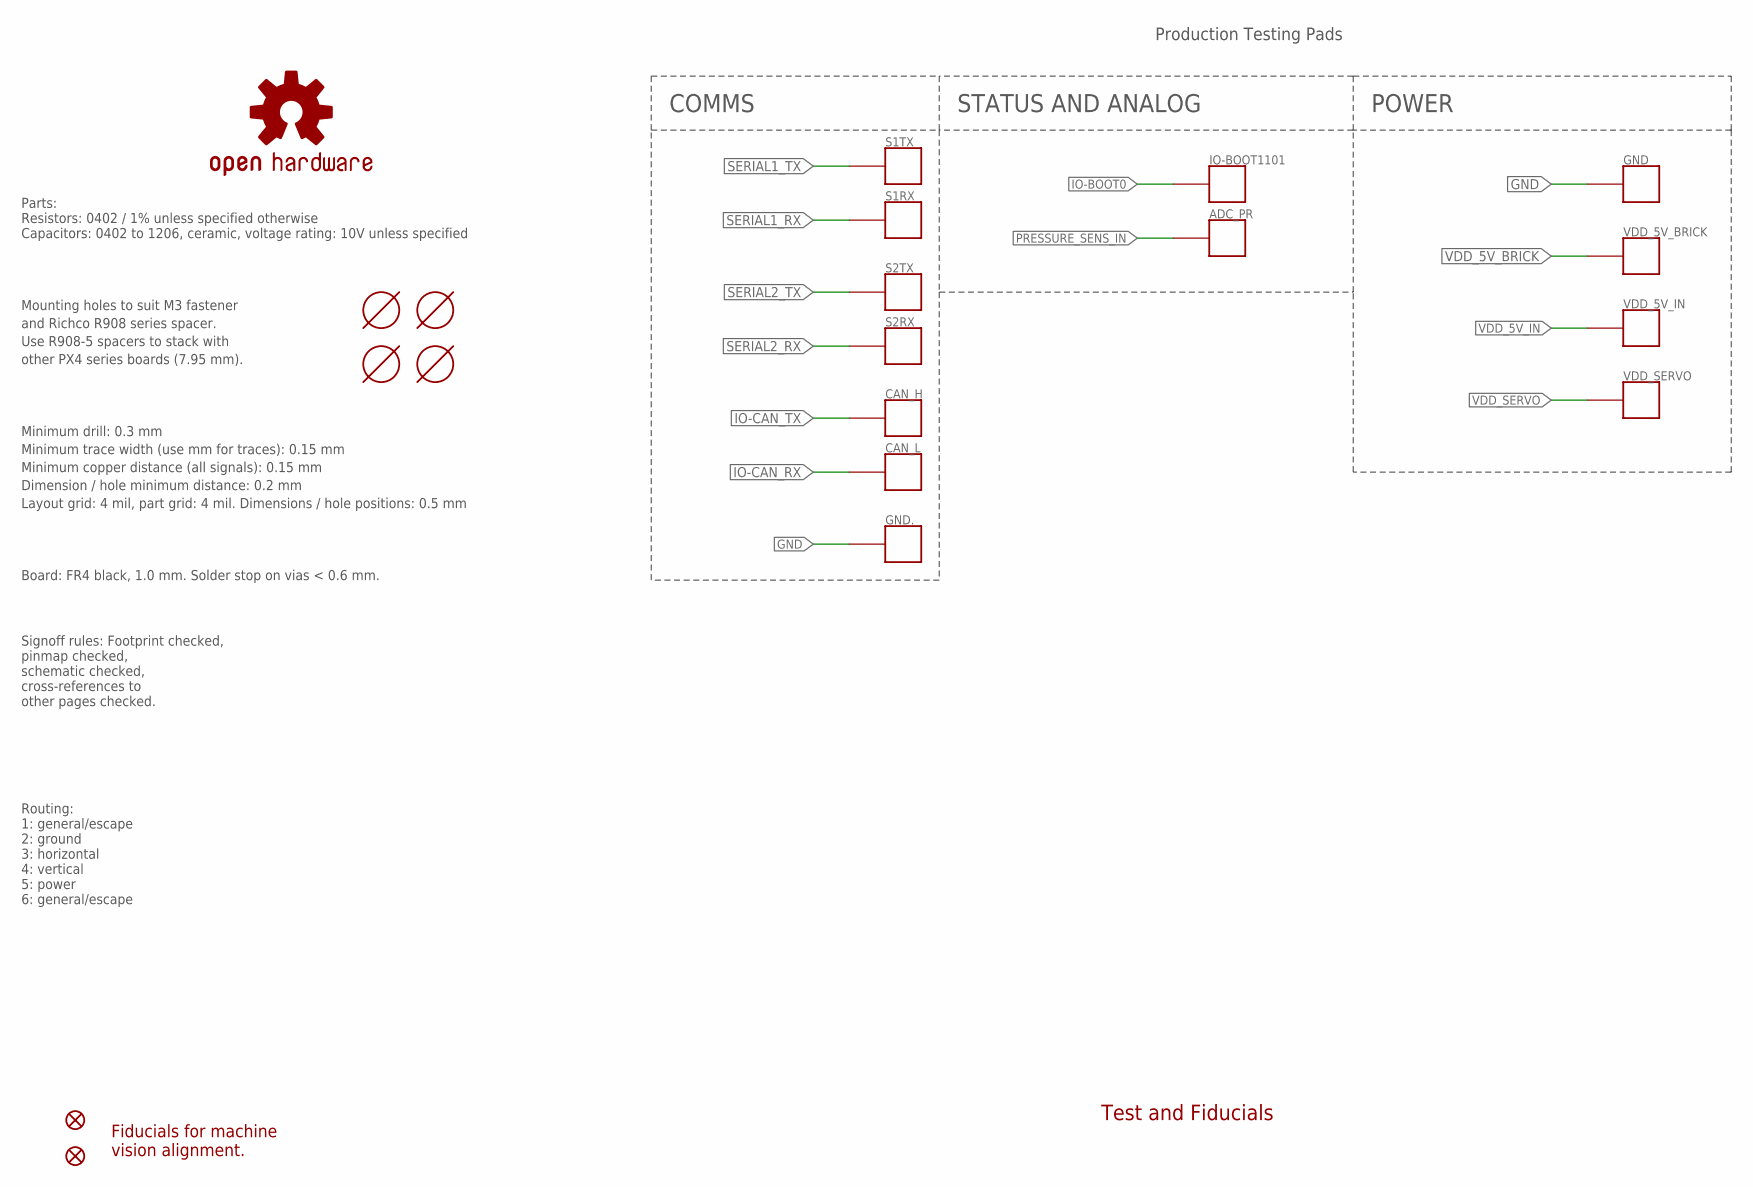
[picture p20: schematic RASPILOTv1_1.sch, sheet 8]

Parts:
ADC_PR: PAD.04; PAD.04X.04; PARTNO *
CAN_H: PAD.04; PAD.04X.04; PARTNO *
CAN_L: PAD.04; PAD.04X.04; PARTNO *
GND, GND.: PAD.04; PAD.04X.04; PARTNO *
IO-BOOT1101: PAD.04; PAD.04X.04; PARTNO *
JP1, JP2: FIDUCIAL1.5X3; FIDUCIAL-1.5X3; PARTNO *
M3_MOUNT1101, M3_MOUNT1102, M3_MOUNT1103, M3_MOUNT1104: MOUNT-HOLE3.1MM; MOUNT-HOLE3.1; PARTNO *
OSHW_LOGO: OSHW-LOGOS; OSHW-LOGO-S; PARTNO *
S1RX, S1TX, S2RX, S2TX: PAD.04; PAD.04X.04; PARTNO *
VDD_5V_BRICK, VDD_5V_IN: PAD.04; PAD.04X.04; PARTNO *
VDD_SERVO: PAD.04; PAD.04X.04; PARTNO *

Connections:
GND: GND.P$1, GND..P$1; also elsewhere on the board
IO-BOOT0: IO-BOOT1101.P$1; also elsewhere on the board
IO-CAN_RX: CAN_L.P$1; also elsewhere on the board
IO-CAN_TX: CAN_H.P$1; also elsewhere on the board
PRESSURE_SENS_IN: ADC_PR.P$1; also elsewhere on the board
SERIAL1_RX: S1RX.P$1; also elsewhere on the board
SERIAL1_TX: S1TX.P$1; also elsewhere on the board
SERIAL2_RX: S2RX.P$1; also elsewhere on the board
SERIAL2_TX: S2TX.P$1; also elsewhere on the board
VDD_5V_BRICK: VDD_5V_BRICK.P$1; also elsewhere on the board
VDD_5V_IN: VDD_5V_IN.P$1; also elsewhere on the board
VDD_SERVO: VDD_SERVO.P$1; also elsewhere on the board

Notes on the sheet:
Mounting holes to suit M3 fastener
and Richco R908 series spacer.
Use R908-5 spacers to stack with
other PX4 series boards (7.95 mm).
Production Testing Pads
Test and Fiducials
Minimum drill: 0.3 mm
Minimum trace width (use mm for traces): 0.15 mm
Minimum copper distance (all signals): 0.15 mm
Dimension / hole minimum distance: 0.2 mm
Layout grid: 4 mil, part grid: 4 mil. Dimensions / hole positions: 0.5 mm
Board: FR4 black, 1.0 mm. Solder stop on vias < 0.6 mm.
Signoff rules: Footprint checked, pinmap checked, schematic checked, cross-references to other pages checked.
Routing: 1: general/escape 2: ground 3: horizontal 4: vertical 5: power 6: general/escape
Fiducials for machine vision alignment.
Parts: Resistors: 0402 / 1% unless specified otherwise Capacitors: 0402 to 1206, ceramic, voltage rating: 10V unless specified
COMMS
POWER
STATUS AND ANALOG

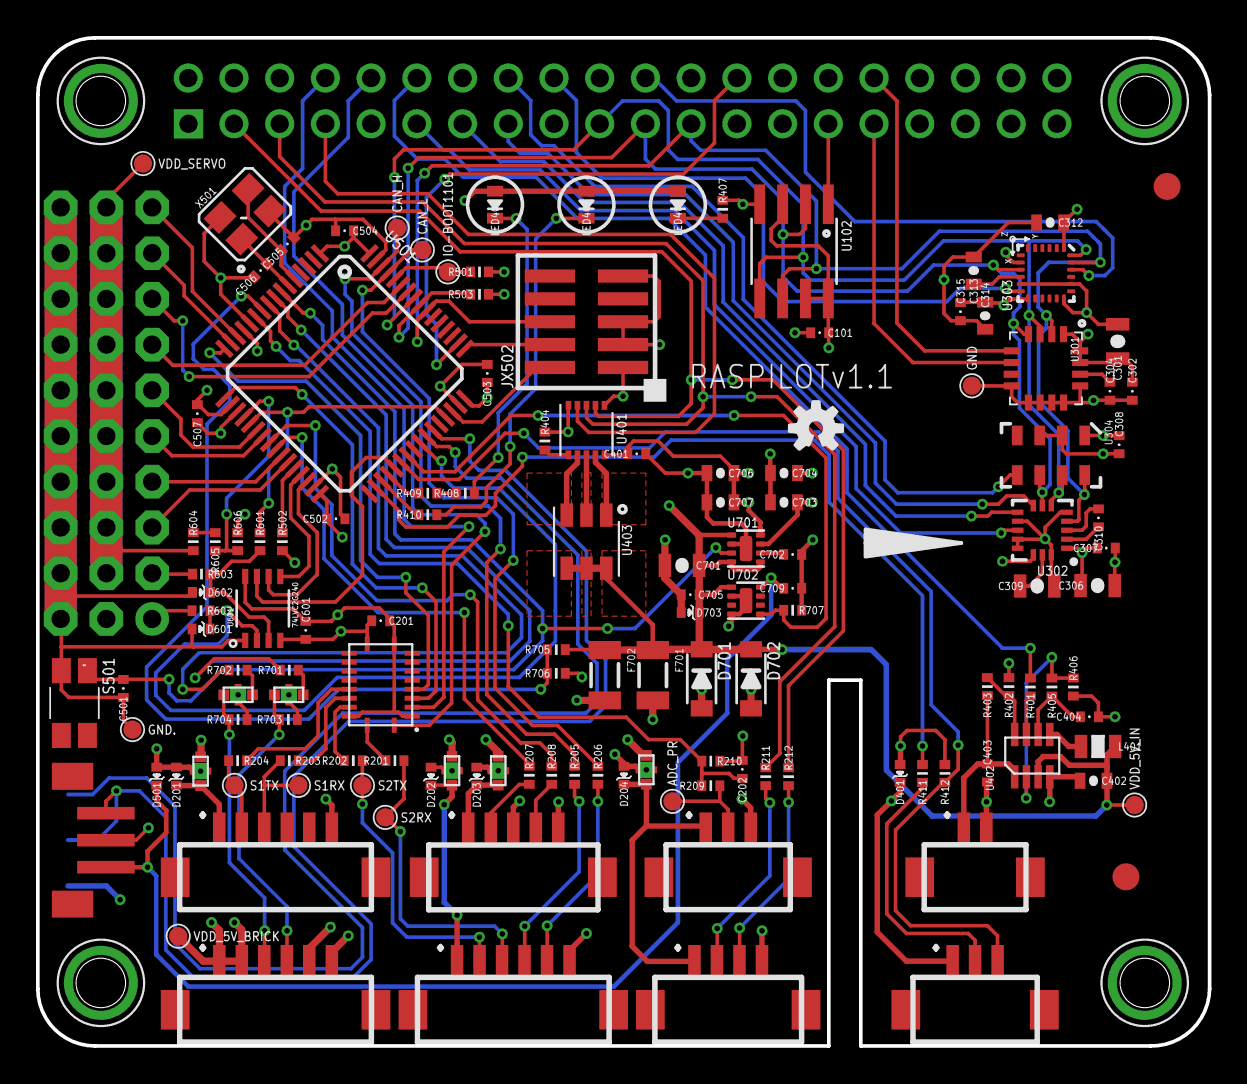
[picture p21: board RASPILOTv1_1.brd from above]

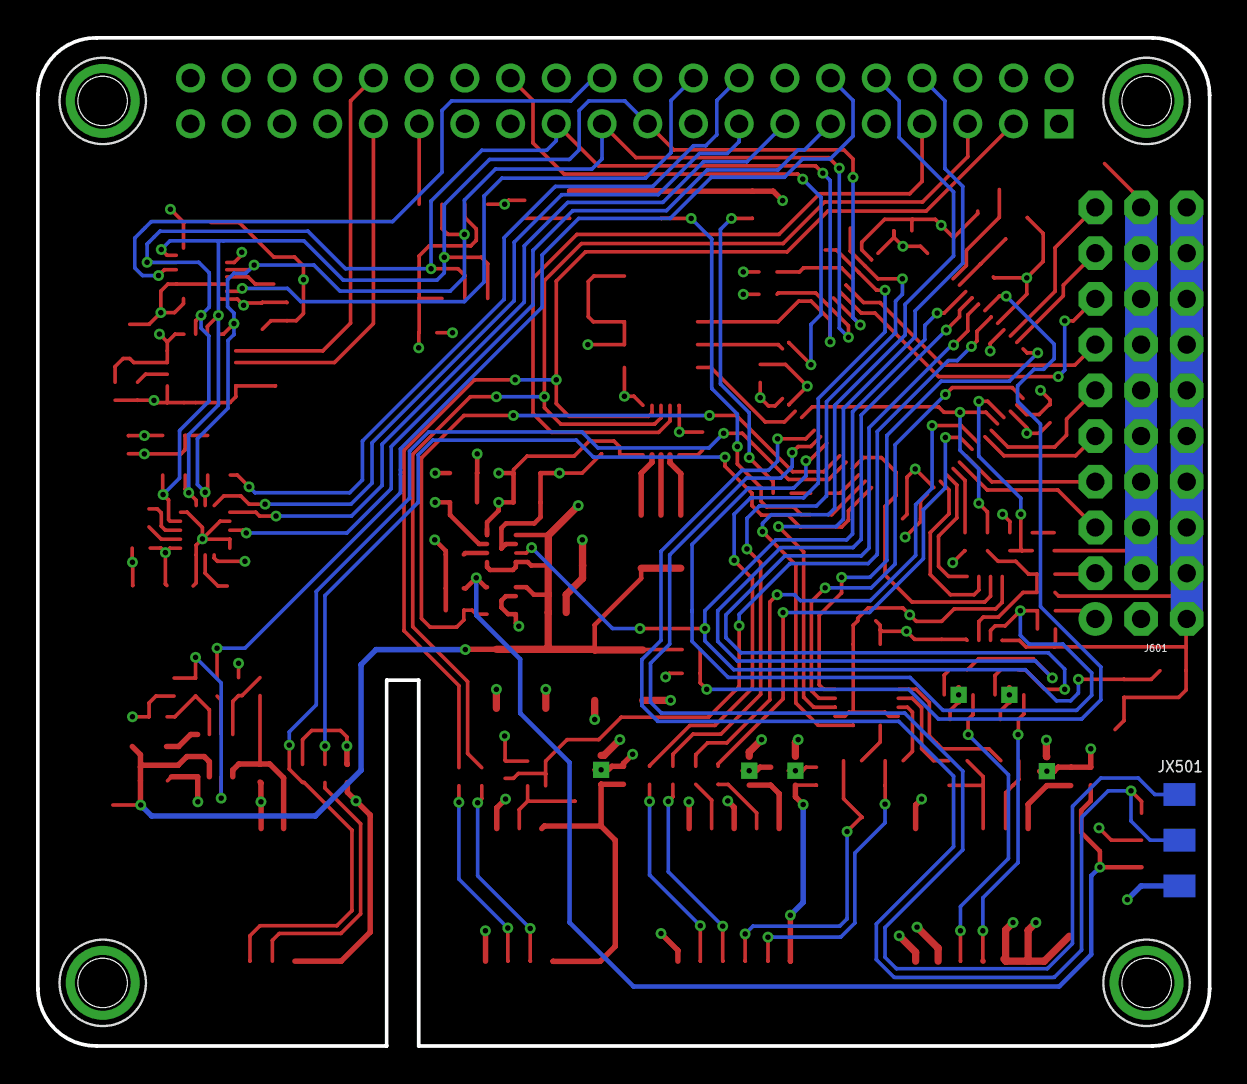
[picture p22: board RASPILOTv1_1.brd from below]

Board: 4 copper layers, 65.1 x 56.0 mm, 146 parts (2 on the bottom side), 114 nets.

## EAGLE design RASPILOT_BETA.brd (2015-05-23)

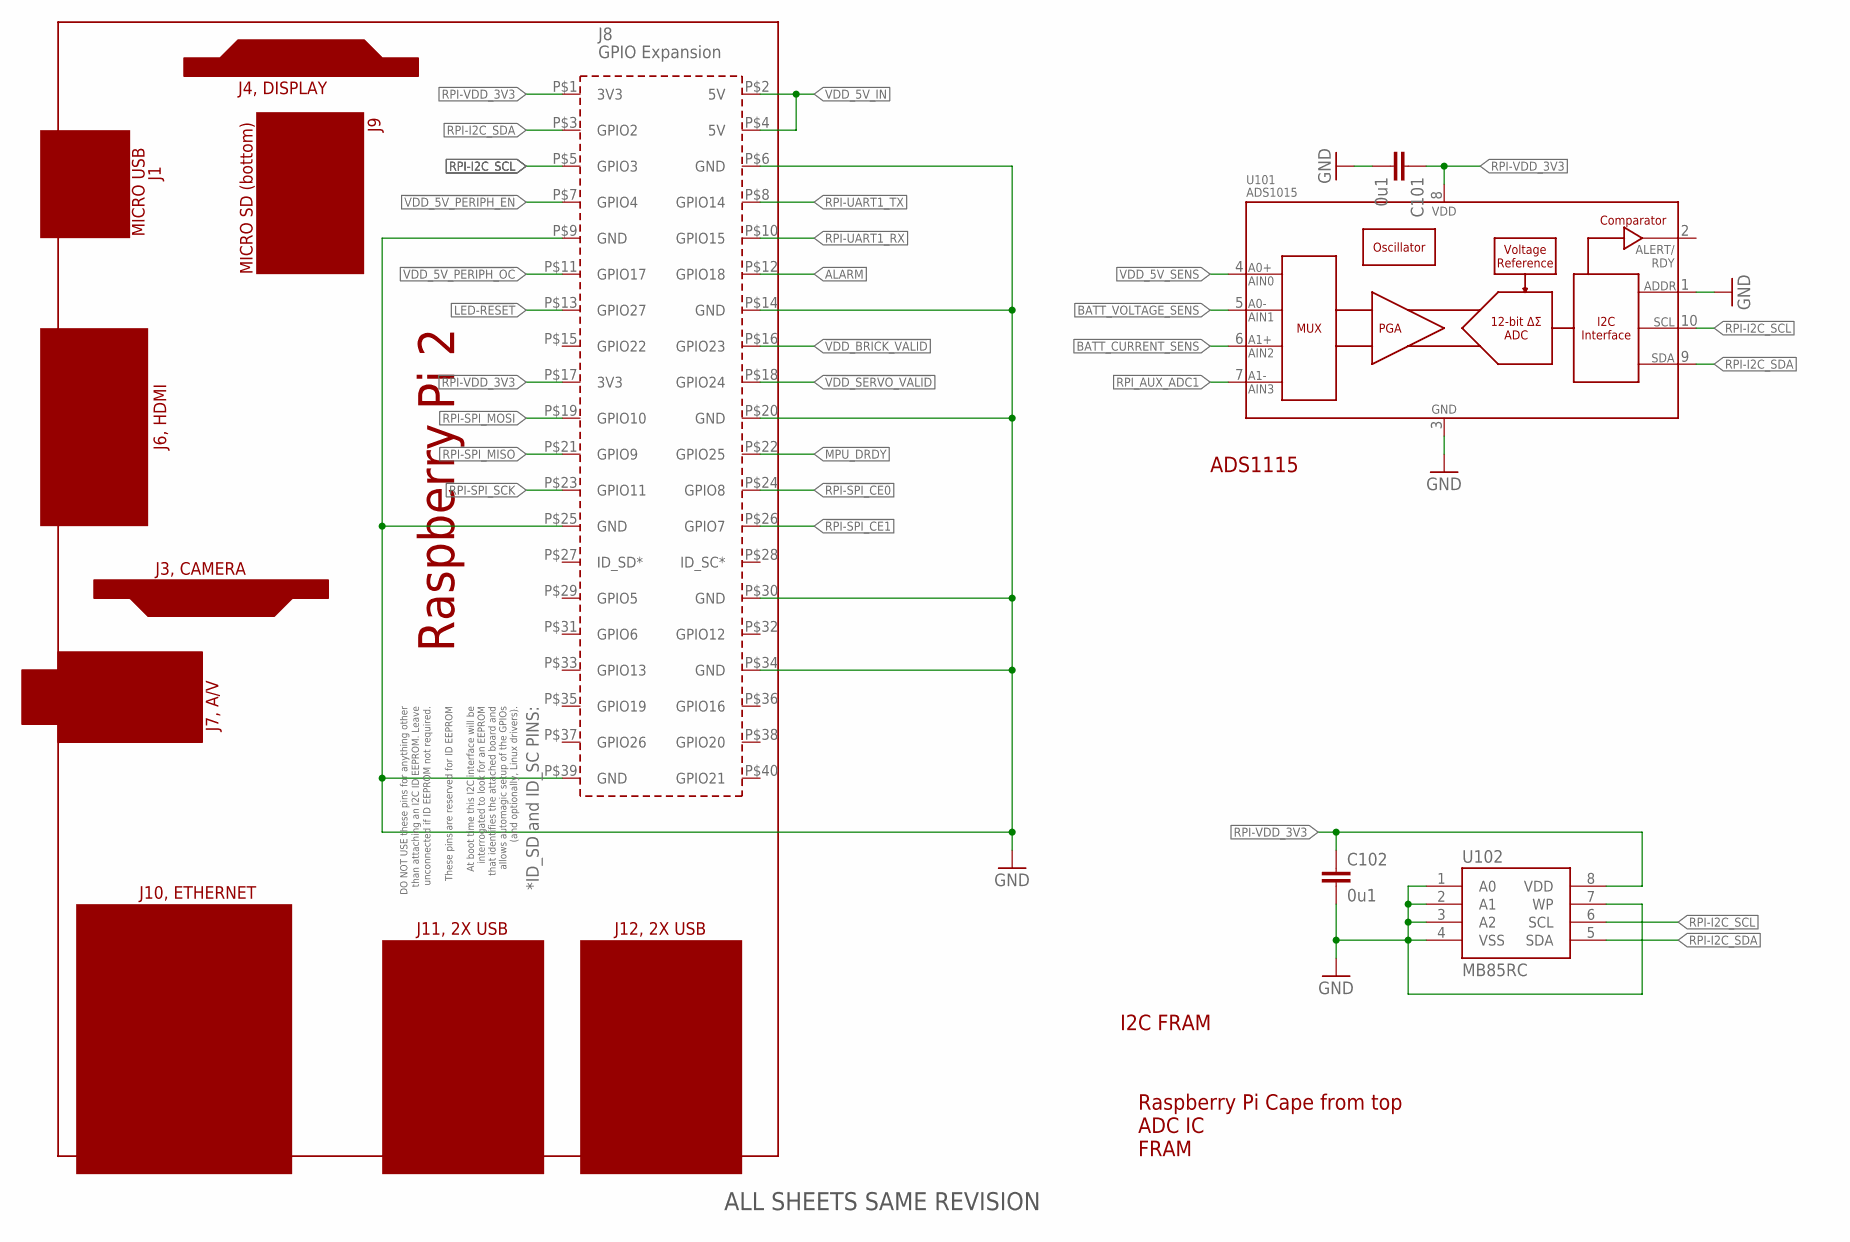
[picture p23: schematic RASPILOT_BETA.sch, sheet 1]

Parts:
C101, C102: 0u1; 0402-CAP; PARTNO CC0402ZRY5V7BB104
J101: RPI2
U101: ADS1015; MSOP10
U102: MB85RC; SOP8

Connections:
!RPI-SPI_CE0: J101.P$24 (GPIO8); also elsewhere on the board
!RPI-SPI_CE1: J101.P$26 (GPIO7); also elsewhere on the board
!VDD_5V_PERIPH_EN: J101.P$7 (GPIO4); also elsewhere on the board
!VDD_5V_PERIPH_OC: J101.P$11 (GPIO17); also elsewhere on the board
!VDD_BRICK_VALID: J101.P$16 (GPIO23); also elsewhere on the board
!VDD_SERVO_VALID: J101.P$18 (GPIO24); also elsewhere on the board
ALARM: J101.P$12 (GPIO18); also elsewhere on the board
BATT_CURRENT_SENS: U101.6 (AIN2); also elsewhere on the board
BATT_VOLTAGE_SENS: U101.5 (AIN1); also elsewhere on the board
GND: C101.P$2 (2), C102.P$2 (2), J101.P$6 (GND), J101.P$9 (GND), J101.P$14 (GND), J101.P$20 (GND), J101.P$25 (GND), J101.P$30 (GND), J101.P$34 (GND), J101.P$39 (GND), U101.1 (ADDR), U101.3 (VSS), U102.1 (A0), U102.2 (A1), U102.3 (A2), U102.4 (VSS), U102.7 (WP); also elsewhere on the board
LED-!RESET: J101.P$13 (GPIO27); also elsewhere on the board
MPU_DRDY: J101.P$22 (GPIO25); also elsewhere on the board
RPI-I2C_SCL: J101.P$5 (GPIO3), U101.10 (SCL), U102.6 (SCL); also elsewhere on the board
RPI-I2C_SDA: J101.P$3 (GPIO2), U101.9 (SDA), U102.5 (SDA); also elsewhere on the board
RPI-SPI_MISO: J101.P$21 (GPIO9); also elsewhere on the board
RPI-SPI_MOSI: J101.P$19 (GPIO10); also elsewhere on the board
RPI-SPI_SCK: J101.P$23 (GPIO11); also elsewhere on the board
RPI-UART1_RX: J101.P$10 (GPIO15); also elsewhere on the board
RPI-UART1_TX: J101.P$8 (GPIO14); also elsewhere on the board
RPI-VDD_3V3: C101.P$1 (1), C102.P$1 (1), J101.P$1 (3V3), J101.P$17 (3V3), U101.8 (VDD), U102.8 (VDD); also elsewhere on the board
RPI_AUX_ADC1: U101.7 (AIN3); also elsewhere on the board
VDD_5V_IN: J101.P$2 (5V), J101.P$4 (5V); also elsewhere on the board
VDD_5V_SENS: U101.4 (AIN0); also elsewhere on the board

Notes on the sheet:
Raspberry Pi Cape from top ADC IC FRAM
ALL SHEETS SAME REVISION
ADS1115
I2C FRAM

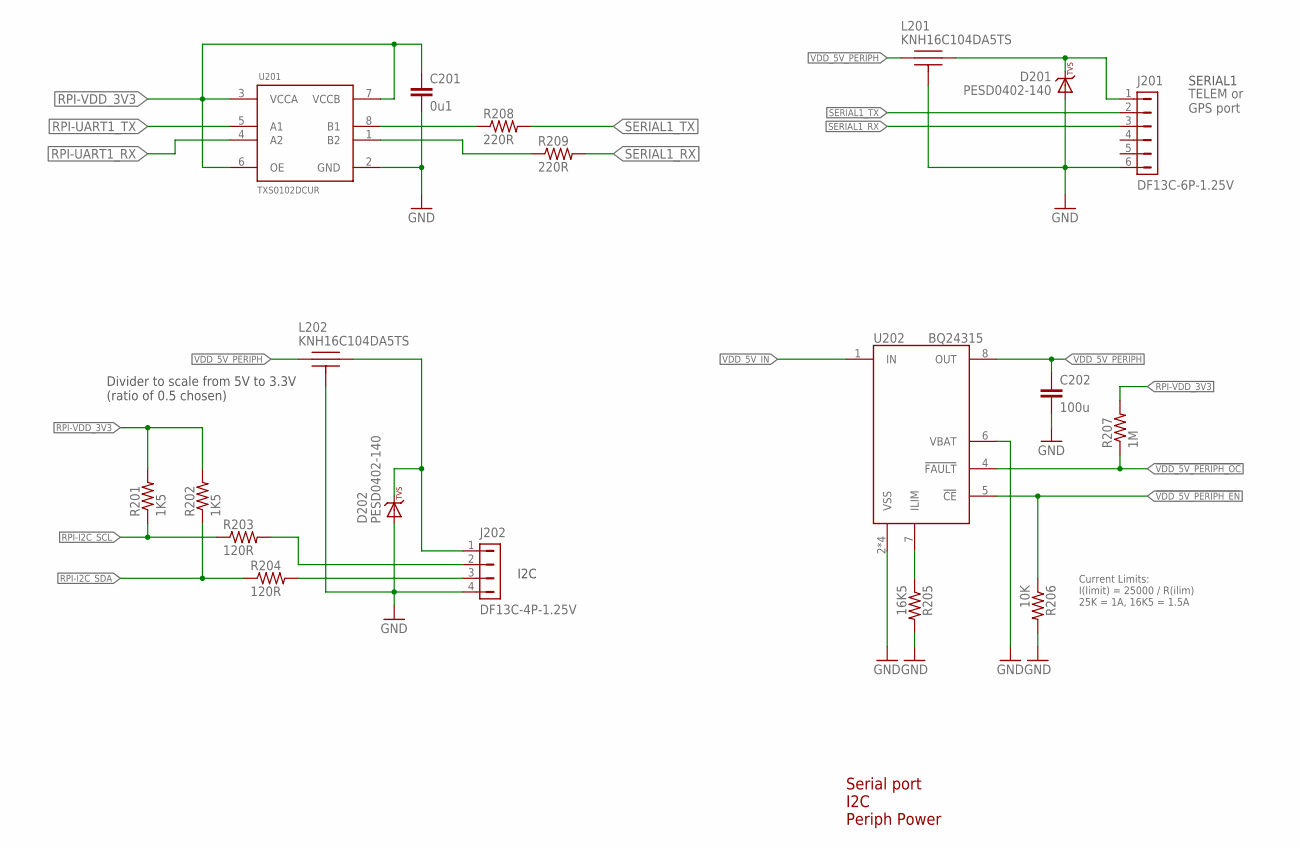
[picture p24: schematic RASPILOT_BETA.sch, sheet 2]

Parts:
C201: 0u1; 0402-CAP; PARTNO CC0402ZRY5V7BB104
C202: 100u; 1206-CAP; PARTNO C3216X5R1A107M160AC
D201, D202: PESD0402-140; 0402-TVS; PARTNO PESD0402-140
J201: DF13C-6P-1.25V; PARTNO DF13C-6P-1.25V(20)
J202: DF13C-4P-1.25V; PARTNO DF13C-4P-1.25V(20)
L201, L202: KNH16C104DA5TS; KYOCERA-KNH16-DA; PARTNO KNH16C104DA5TS
R201, R202: 1K5; 0402-RES; PARTNO RC0402FR-071K5L
R203, R204: 120R; 0402-RES; PARTNO RC0402FR-07120RL
R205: 16K5; 0402-RES; PARTNO RMCF0402FT25K5
R206: 10K; 0402-RES; PARTNO RC0402FR-0710KL
R207: 1M; 0402-RES; PARTNO RC0402FR-071ML
R208, R209: 220R; 0402-RES; PARTNO RC0402FR-07220RL
U201: TXS0102DCUR; TI-DCU
U202: BQ24315; QFN8-DSG; PARTNO BQ24315DSGR

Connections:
!VDD_5V_PERIPH_EN: R206.P$1 (1), U202.5 (!CE); also elsewhere on the board
!VDD_5V_PERIPH_OC: R207.P$1 (1), U202.4 (!FAULT); also elsewhere on the board
GND: C201.P$2 (2), C202.P$2 (2), D201.A, D202.A, J201.6, J202.4, L201.P$3, L201.P$4, L201.P$5, L202.P$3, L202.P$4, L202.P$5, R205.P$2 (2), R206.P$2 (2), U201.2 (GND), U202.2 (VSS), U202.6 (VBAT), U202.GND (VSS), U202.P$2 (VSS), U202.P$3 (VSS); also elsewhere on the board
unnamed: J202.2, R203.P$2 (2)
unnamed: J202.3, R204.P$2 (2)
unnamed: D202.C, J202.1, L202.P$2
unnamed: R208.P$1 (1), U201.8 (B1)
unnamed: R209.P$1 (1), U201.1 (B2)
unnamed: R205.P$1 (1), U202.7 (ILIM)
unnamed: D201.C, J201.1, L201.P$2
RPI-I2C_SCL: R201.P$1 (1), R203.P$1 (1); also elsewhere on the board
RPI-I2C_SDA: R202.P$1 (1), R204.P$1 (1); also elsewhere on the board
RPI-UART1_RX: U201.4 (A2); also elsewhere on the board
RPI-UART1_TX: U201.5 (A1); also elsewhere on the board
RPI-VDD_3V3: C201.P$1 (1), R201.P$2 (2), R202.P$2 (2), R207.P$2 (2), U201.3 (VCCA), U201.6 (OE), U201.7 (VCCB); also elsewhere on the board
SERIAL1_RX: J201.3, R209.P$2 (2); also elsewhere on the board
SERIAL1_TX: J201.2, R208.P$2 (2); also elsewhere on the board
VDD_5V_IN: U202.1 (IN); also elsewhere on the board
VDD_5V_PERIPH: C202.P$1 (1), L201.P$1, L202.P$1, U202.8 (OUT)

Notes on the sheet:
Serial port I2C Periph Power
SERIAL1
TELEM or GPS port
I2C
Divider to scale from 5V to 3.3V (ratio of 0.5 chosen)
Current Limits: I(limit) = 25000 / R(ilim) 25K = 1A, 16K5 = 1.5A


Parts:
C301: 0u01; 0402-CAP; PARTNO CC0402ZRY5V7BB104
C302, C304, C305, C308, C309: 0u1; 0402-CAP; PARTNO CC0402ZRY5V7BB104
C303: 2u2; 0603-CAP; PARTNO C1608X6S1C225K080AC
C306: 4u7; 0603-CAP; PARTNO C1608X6S1C225K080AC
C307: 0u22; 0402-CAP; PARTNO CC0402ZRY5V7BB104
D301: DIODE-0603; 0603-DIO
J301: RF-MCX; RF-MCX-H
L301: 100nH; 0603-IND
R301: 10R; 0603-RES
R302: 1K; 0402-RES; PARTNO RMCF0402FT16K5
SJ301: SOLDERJUMPERNC; SJ_2S
U301: MPU-6500
U302: HMC5883L; HMC5883L-MAN
U303: MS5611-01BA; PARTNO MS5611-01BA
U304: NEO-M8N
UB301: MS621FE

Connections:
!RPI-SPI_CE0: U304.18 (SDA); also elsewhere on the board
!RPI-SPI_CE1: U301.22 (!CS); also elsewhere on the board
GND: C301.P$2 (2), C302.P$2 (2), C303.P$2 (2), C304.P$2 (2), C305.P$2 (2), C306.P$2 (2), C308.P$2 (2), C309.P$2 (2), J301.1 (GND), J301.2 (GND), J301.3 (GND), J301.4 (GND), U301.11 (FSYNC), U301.18 (GND), U301.20 (RESV), U302.9 (GND1), U302.11 (GND2), U303.3 (GND), U303.5 (CSB2), U304.2 (D_SEL), U304.10 (GND), U304.12 (GND), U304.13 (GND), U304.24 (GND), UB301.2 (NEG); also elsewhere on the board
MPU_DRDY: U301.12 (INT); also elsewhere on the board
unnamed: C302.P$1 (1), U301.10 (REGOUT)
unnamed: C306.P$1 (1), U302.10 (C1)
unnamed: C307.P$1 (1), U302.8 (SETP)
unnamed: C307.P$2 (2), U302.12 (SETC)
unnamed: SJ301.1, U302.16 (SDA)
unnamed: J301.5 (RF), L301.P$1 (1), U304.11 (RF_IN)
unnamed: R302.P$2 (2), U304.22 (V_BCKP), UB301.1 (POS)
unnamed: R301.1, U304.9 (VCC_RF)
unnamed: L301.P$2 (2), R301.2
unnamed: D301.C, R302.P$1 (1)
RPI-I2C_SCL: U302.1 (SCL), U303.8 (SCLK); also elsewhere on the board
RPI-I2C_SDA: SJ301.2, U303.7 (SDI/SDA); also elsewhere on the board
RPI-SPI_MISO: U301.9 (AD0/SDO), U304.20 (TXD); also elsewhere on the board
RPI-SPI_MOSI: U301.24 (SDA/SDI), U304.21 (RXD); also elsewhere on the board
RPI-SPI_SCK: U301.23 (SCL/SCLK), U304.19 (SCL); also elsewhere on the board
RPI-VDD_3V3: C301.P$1 (1), C303.P$1 (1), C304.P$1 (1), C305.P$1 (1), C308.P$1 (1), C309.P$1 (1), D301.A, U301.1 (NC), U301.8 (VDDIO), U301.13 (VDD), U302.2 (VDD), U302.4 (S1_VDDIO), U302.13 (VDDIO), U303.1 (VDD), U303.2 (PS), U304.23 (VCC); also elsewhere on the board

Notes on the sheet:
Sensors GPS
MPU6500/9250


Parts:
C401: 0u1; 0402-CAP; PARTNO CC0402ZRY5V7BB104
D401: PESD0402-140; 0402-TVS; PARTNO PESD0402-140
J401: DF13C-3P-1.25V; PARTNO DF13C-3P-1.25V(20)
LED402: GREEN; 0603-LED; PARTNO APTD1608CGCK
LED403: AMBER; 0603-LED; PARTNO APTD1608SECK
LED405: BLUE; 0603-LED; PARTNO APTD1608QBC/D
Q401: MOSFET-NCHANNELSMD; SOT23-3
R401, R402: 10K; 0402-RES; PARTNO RC0402FR-0710KL
R403: 220R; 0402-RES; PARTNO RMCF0402FT16K5
R404: 220R; 0402-RES; PARTNO RMCF0402FT9K09
R405: 10K; 0402-RES; PARTNO RMCF0402FT9K09
R409, R410, R411, R412: 220R; 0402-RES; PARTNO RC0402FR-07220RL
R413: 68R; 0402-RES; PARTNO ERJ-2GEJ680X
R414: 1K5; 0402-RES; PARTNO RC0402FR-071K5L
SG401: BUZZER; F/TMB
U401: TCA62724FMG; SON10; PARTNO TCA62724FMG
U402: LRTB GFTG-T7AW-1+V7A7-29+R5T9-49-L; 6-PLCC; PARTNO LRTB GFTG-T7AW-1+V7A7-29+R5T9-49-L

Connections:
!IO-LED_AMBER: R411.P$1 (1); also elsewhere on the board
!IO-LED_BLUE: R412.P$1 (1); also elsewhere on the board
!IO-LED_SAFETY: R413.P$2 (2); also elsewhere on the board
ALARM: R404.P$2 (2); also elsewhere on the board
GND: C401.P$2 (2), D401.A, Q401.2 (S), R401.P$1 (1), R402.P$1 (1), R405.P$2 (2), R409.P$1 (1), R414.P$2 (2), U401.5 (GND); also elsewhere on the board
IO-VDD_3V3: D401.C, J401.1; also elsewhere on the board
IO-VDD_5V5: LED402.A, LED403.A, LED405.A; also elsewhere on the board
LED-!RESET: R401.P$2 (2), U401.4 (!RESET); also elsewhere on the board
unnamed: Q401.1 (G), R404.P$1 (1), R405.P$1 (1)
unnamed: LED405.C, R412.P$2 (2)
unnamed: R403.P$1 (1), SG401.+
unnamed: Q401.3 (D), SG401.-
unnamed: LED402.C, R409.P$2 (2)
unnamed: R410.P$1 (1), R411.P$2 (2)
unnamed: LED403.C, R410.P$2 (2)
unnamed: J401.2, R413.P$1 (1)
unnamed: R402.P$2 (2), U401.6 (REXT)
RGB_LED_3: U401.9 (OUT0), U402.C1 (C)
RGB_LED_4: U401.8 (OUT1), U402.C2 (C)
RGB_LED_14: U401.7 (OUT2), U402.C3 (C)
RPI-I2C_SCL: U401.3 (SCL); also elsewhere on the board
RPI-I2C_SDA: U401.2 (SDA); also elsewhere on the board
RPI-VDD_3V3: C401.P$1 (1), U401.1 (!SHDN), U401.10 (VIN); also elsewhere on the board
SAFETY: J401.3, R414.P$1 (1); also elsewhere on the board
VDD_5V_IN: R403.P$2 (2), U402.A1 (A), U402.A2 (A), U402.A3 (A); also elsewhere on the board

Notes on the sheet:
LEDs Piezo driver Safety switch
Switch: E-Switch LP1OA1AR
SAFETY
LED should be Omron LRTBG6SG-U4AA-1+V2B4-25+S or similar 6PLCC high-brigtness type.
Iout = (1.17 / REXT) * 460 10K = 54mA, selected for maximum daylight visibility.
All LEDs nominal target 60mcd for good daylight visibility. Resistor values have been adjusted to optimize BOM. Green: APG1608CGKC/T Vf(typ): 2.1V Target If: 20mA Selected R: 220 Cacluated If @ 5.5V: 15mA Amber: APT1608SECK Vf(typ): 2.1V Target If: 5mA Selected R: 440 Cacluated If @ 5.5V: 8mA Blue: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

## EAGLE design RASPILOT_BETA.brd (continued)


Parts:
C501, C502, C503, C504: 0u1; 0402-CAP; PARTNO CC0402ZRY5V7BB104
C505, C506: 8p; 0402-CAP; PARTNO C1005C0G1H080C
D501: PESD0402-140; 0402-TVS; PARTNO PESD0402-140
J501: JST-ZH-3; JST-ZH-SMT-VERTICAL; PARTNO B3B-ZR-SM4-TF (LF)(SN)(P)
JX501: HEADER-3X1BOARDEDGE-SHORT; HEADER_3X01_SMD_H_BOARD_EDGE_SHORT
JX502: ARM_MINI_JTAG-SMT; FTSH-105-01-XXX-DV-K; PARTNO M50-3900542
R501, R502: 220R; 0402-RES; PARTNO RC0402FR-07220RL
R503, R506: 10K; 0402-RES; PARTNO RC0402FR-0710KL
R504, R505: 120R; 0402-RES; PARTNO RC0402FR-07220RL
S501: RESET; EVQP7J01K; PARTNO EVQ-P7J01P
U501: STM32F10XCXT6; TQFP48; PARTNO STM32F100C8T6B
X501: 3.2x2.5 mm / 8 MHz / 15 ppm; OSCILLATOR-3.2X2.5; PARTNO NX3225SA-24.000000MHZ

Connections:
!IO-LED_AMBER: U501.28 (PB15); also elsewhere on the board
!IO-LED_BLUE: U501.27 (PB14); also elsewhere on the board
!IO-LED_SAFETY: U501.26 (PB13); also elsewhere on the board
GND: C501.P$1 (1), C502.P$2 (2), C503.P$2 (2), C504.P$2 (2), C505.P$2 (2), C506.P$1 (1), D501.A, J501.P$2, JX501.3 (GND), JX502.3, JX502.5, JX502.9, R503.P$2 (2), R506.P$2 (2), S501.B3 (2), U501.8 (VSSA), U501.23 (VSS_1), U501.35 (VSS_2), U501.47 (VSS_3), X501.2 (NC_2), X501.4 (NC_4); also elsewhere on the board
IO-!RESET: C501.P$2 (2), S501.A1 (1), U501.7 (NRST); also elsewhere on the board
IO-!VDD_SERVO_IN_FAULT: U501.38 (PA15); also elsewhere on the board
IO-BOOT0: R506.P$1 (1), U501.44 (BOOT0); also elsewhere on the board
IO-BOOT1: R503.P$1 (1), U501.20 (PB2)
IO-CH1: U501.10 (PA0); also elsewhere on the board
IO-CH2: U501.11 (PA1); also elsewhere on the board
IO-CH3: U501.45 (PB8); also elsewhere on the board
IO-CH4: U501.46 (PB9); also elsewhere on the board
IO-CH5: U501.16 (PA6); also elsewhere on the board
IO-CH6: U501.17 (PA7); also elsewhere on the board
IO-CH7: U501.18 (PB0); also elsewhere on the board
IO-CH8: U501.19 (PB1); also elsewhere on the board
IO-SWCLK: JX502.4, U501.37 (PA14)
IO-SWDIO: JX502.2, U501.34 (PA13)
IO-SWO: JX502.6, U501.39 (PB3)
IO-USART1_RX: J501.P$3, U501.31 (PA10)
IO-USART1_TX: U501.30 (PA9)
IO-USART2_RX: JX501.2 (+5V), R502.P$2 (2)
IO-USART2_TX: JX501.1 (PPM), R501.P$2 (2)
IO-VDD_3V3: C502.P$1 (1), C503.P$1 (1), C504.P$1 (1), JX502.1, U501.9 (VDDA), U501.24 (VDD_1), U501.36 (VDD_2), U501.48 (VDD_3); also elsewhere on the board
unnamed: R505.P$1 (1), U501.43 (PB7)
unnamed: R504.P$1 (1), U501.42 (PB6)
unnamed: C506.P$2 (2), U501.6 (PD1/OSC=>), X501.1
unnamed: C505.P$1 (1), U501.5 (PD0/OSC<=), X501.3
unnamed: R501.P$1 (1), U501.12 (PA2)
unnamed: R502.P$1 (1), U501.13 (PA3)
PPM_INPUT: U501.29 (PA8); also elsewhere on the board
RPI-I2C_SCL: R504.P$2 (2); also elsewhere on the board
RPI-I2C_SDA: R505.P$2 (2); also elsewhere on the board
SAFETY: U501.41 (PB5); also elsewhere on the board
SBUS_INPUT: U501.22 (PB11); also elsewhere on the board
VBAT: U501.1 (VBAT)
VDD_3V3_SPEKTRUM: D501.C, J501.P$1; also elsewhere on the board
VDD_3V3_SPEKTRUM_EN: U501.2 (PC13); also elsewhere on the board
VDD_SERVO_SENS: U501.14 (PA4); also elsewhere on the board

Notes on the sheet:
IO SoC Ports Spektrum/DSM port
LED3 moves to PB13 to make room for S.Bus output
IO_SERIAL1
Spektrum/DSM
Timer allocation: PA0: TIM2_CH1: IO-CH1 PA1: TIM2_CH2: IO-CH2 PB8: TIM4_CH3: IO-CH3 PB9: TIM4_CH4: IO-CH4 PA6: TIM3_CH1: IO-CH5 PA7: TIM3_CH2: IO-CH6 PB0: TIM3_CH3: IO-CH7 PB1: TIM3_CH4: IO-CH8 PA8: TIM1_CH1: PPM_IN PA11: TIM1_CH4: RSSI_IN
spare pwm
spare gpio


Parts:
C601, C602: 0u1; 0402-CAP; PARTNO CC0402ZRY5V7BB104
D601, D603: PESD0402-140; 0402-TVS; PARTNO PESD0402-140
D602: MSS1P4-M3; MICROSMP; PARTNO MSS1P4-M3/89A
J601: HEADER-3X10; 3X10RA
L601: KNH16C104DA5TS; KYOCERA-KNH16-DA; PARTNO KNH16C104DA5TS
R601, R602, R603, R604, R605, R606, R607, R608, R609: 220R; 0402-RES; PARTNO RC0402FR-07220RL
R610, R611, R612: 10K/0.1%; 0402-RES; PARTNO ERA-2AEB103X
U601: TXS0108QFN20; QFN20-RGY; PARTNO TXS0108ERGYR
U602: 74LVC1G125-SOT353; SOT353

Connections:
GND: C601.P$2 (2), C602.P$2 (2), D601.A, D603.A, J601.3 (GND), J601.6 (GND), J601.9 (GND), J601.12 (GND), J601.15 (GND), J601.18 (GND), J601.21 (GND), J601.24 (GND), J601.27 (GND), J601.30 (GND), L601.P$3, L601.P$4, L601.P$5, R612.P$1 (1), U601.11 (GND), U602.1 (!OE), U602.3 (GND); also elsewhere on the board
IO-CH1: U601.9 (A8); also elsewhere on the board
IO-CH2: U601.8 (A7); also elsewhere on the board
IO-CH3: U601.7 (A6); also elsewhere on the board
IO-CH4: U601.6 (A5); also elsewhere on the board
IO-CH5: U601.5 (A4); also elsewhere on the board
IO-CH6: U601.4 (A3); also elsewhere on the board
IO-CH7: U601.3 (A2); also elsewhere on the board
IO-CH8: U601.1 (A1); also elsewhere on the board
IO-VDD_3V3: C601.P$1 (1), C602.P$1 (1), U601.2 (VCCA), U601.10 (OE), U601.19 (VCCB), U602.5 (VCC); also elsewhere on the board
unnamed: R610.P$1 (1), R611.P$2 (2)
unnamed: J601.7 (PWM_8), R601.P$2 (2)
unnamed: R601.P$1 (1), U601.20 (B1)
unnamed: R602.P$1 (1), U601.18 (B2)
unnamed: R603.P$1 (1), U601.17 (B3)
unnamed: R604.P$1 (1), U601.16 (B4)
unnamed: R605.P$1 (1), U601.15 (B5)
unnamed: R606.P$1 (1), U601.14 (B6)
unnamed: R607.P$1 (1), U601.13 (B7)
unnamed: R608.P$1 (1), U601.12 (B8)
unnamed: J601.10 (PWM_7), R602.P$2 (2)
unnamed: J601.28 (PWM_1), R608.P$2 (2)
unnamed: J601.25 (PWM_2), R607.P$2 (2)
unnamed: J601.22 (PWM_3), R606.P$2 (2)
unnamed: J601.19 (PWM_4), R605.P$2 (2)
unnamed: J601.16 (PWM_5), R604.P$2 (2)
unnamed: J601.13 (PWM_6), R603.P$2 (2)
unnamed: D602.CATHODE (C), D603.C, L601.P$1
PPM-SBUS-PROT: J601.1 (PPM/S.BUS_IN), R609.P$2 (2)
PPM_INPUT: D601.C, R609.P$1 (1), U602.2 (A); also elsewhere on the board
RX-VDD_5V5: J601.2 (5V); also elsewhere on the board
SBUS_INPUT: U602.4 (Y); also elsewhere on the board
VDD_SERVO: D602.ANODE (A), J601.5 (5V), J601.8 (5V), J601.11 (5V), J601.14 (5V), J601.17 (5V), J601.20 (5V), J601.23 (5V), J601.26 (5V), J601.29 (5V), R610.P$2 (2); also elsewhere on the board
VDD_SERVO_IN: L601.P$2; also elsewhere on the board
VDD_SERVO_SENS: R611.P$1 (1), R612.P$2 (2); also elsewhere on the board

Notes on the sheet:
Servo Header S.Bus interface
S.Bus input
Servo outputs


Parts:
C701: 10u/25V; 0805-CAP; PARTNO CL21A106KAYNNNE
C702: 10n; 0402-CAP; PARTNO CC0402KRX7R7BB103
C703: 1u; 0603-CAP; PARTNO CC0603ZRY5V7BB105
C704: 10u; 0603-CAP; PARTNO C1608X5R1A106K080AC
C705: 0u1; 0402-CAP; PARTNO CC0402ZRY5V7BB104
C706: 2u2; 0402-CAP; PARTNO C1005X6S1C225K050BC
D701, D702: PMEG2005CT; SOT23-3; PARTNO PMEG2005CT
F701: 0ZCA0035FF2G; PTC-1206; PARTNO 0ZCA0035FF2G
R701: 100K; 0402-RES; PARTNO RC0402FR-07100KL
R702: 10K; 0402-RES; PARTNO RC0402FR-0710KL
U701: BQ24313; QFN8-DSG; PARTNO BQ24313DSGT
U702: MIC5332; MLF-8-EPAD; PARTNO MIC5332-SSYMT

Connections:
GND: C701.P$2 (2), C702.P$2 (2), C703.P$2 (2), C704.P$2 (2), C705.P$2 (2), C706.P$2 (2), R701.P$1 (1), R702.P$1 (1), U701.2 (VSS), U701.5 (!CE), U701.6 (VBAT), U701.GND (VSS), U701.P$2 (VSS), U701.P$3 (VSS), U702.2 (GND), U702.GND; also elsewhere on the board
IO-!RESET: U702.3 (POR2); also elsewhere on the board
IO-!VDD_SERVO_IN_FAULT: U701.4 (!FAULT); also elsewhere on the board
IO-VDD_3V3: C703.P$1 (1), C704.P$1 (1), U702.7 (VOUT2); also elsewhere on the board
IO-VDD_5V5: C701.P$1 (1), C705.P$1 (1), D701.3 (CC), U702.1 (VIN), U702.4 (EN2); also elsewhere on the board
unnamed: D701.2 (A2), D702.2 (A2), U701.8 (OUT)
unnamed: R701.P$2 (2), U701.7 (ILIM)
unnamed: D702.3 (CC), F701.2
unnamed: C702.P$1 (1), U702.6 (CSET)
RX-VDD_5V5: F701.1; also elsewhere on the board
VDD_3V3_SPEKTRUM: C706.P$1 (1), U702.8 (VOUT1); also elsewhere on the board
VDD_3V3_SPEKTRUM_EN: R702.P$2 (2), U702.5 (EN1); also elsewhere on the board
VDD_5V_IN: D701.1 (A1), D702.1 (A1); also elsewhere on the board
VDD_SERVO_IN: U701.1 (IN); also elsewhere on the board

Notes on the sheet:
Dual supply from servo rail and FMU 5V rail
Current limit = 25 / Rilim (current in A, R in kOhms) 100K = 250mA
IO Power Supply
Reset output 1s / uF 10n = 10ms delay from power good to reset de-asserted.
Output voltage limited to 5.5V for input voltages up to 10.5V; output switches off at higher input voltages.


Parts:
C801, C802: 22u/25V; 0805-CAP; PARTNO CL21A226MAQNNNE
C803: 100u; 1206-CAP; PARTNO C3216X5R1A107M160AC
C804, C805, C806: 0u1; 0402-CAP; PARTNO C1005X7R1E104K050BB
C807, C808: 10p/25V; 0402-CAP; PARTNO C0402C100J3GACTU
C809: 1000p/25V; 0402-CAP; PARTNO GRM1555C1E102JA01D
J801: DF13C-6P-1.25V; PARTNO DF13C-6P-1.25V(20)
L801, L802: KNH16C104DA5TS; KYOCERA-KNH16-DA; PARTNO KNH16C104DA5TS
R801, R802, R815, R816: 10K/0.1%; 0402-RES; PARTNO ERA-2AEB103X
R803, R804: 1M; 0402-RES; PARTNO RC0402FR-071ML
R805, R808, R811: 453K; 0402-RES; PARTNO RMCF0402FT453K
R806, R809, R812: 56K; 0402-RES; PARTNO ERA-2AEB563X
R807, R810, R813: 105K; 0402-RES; PARTNO ERJ-2RKF1053X
R814: 0R; 0402-RES; PARTNO ERJ-2GE0R00X
RN801: 1M; EXB28V; PARTNO EXB-28V105JX
U801: LTC4417; MO-220; PARTNO LTC4417IUF#PBF
U802, U803: NTHD4102PT1G; 1206-8; PARTNO NTHD4102PT1G

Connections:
!VDD_BRICK_VALID: RN801.4 (1), U801.P$7 (!VALID1); also elsewhere on the board
!VDD_SERVO_VALID: RN801.3 (1), U801.P$8 (!VALID2); also elsewhere on the board
BATT_CURRENT_SENS: R801.P$1 (1); also elsewhere on the board
BATT_CURRENT_SENS_PROT: J801.3, L801.P$1, R804.P$1 (1)
BATT_VOLTAGE_SENS: R802.P$1 (1); also elsewhere on the board
BATT_VOLTAGE_SENS_PROT: J801.4, L802.P$1, R803.P$1 (1)
GND: C801.P$2 (2), C802.P$2 (2), C803.P$2 (2), C804.P$2 (2), C805.P$2 (2), C806.P$2 (2), C807.P$2 (2), C808.P$2 (2), C809.P$2 (2), J801.5, J801.6, L801.P$3, L801.P$4, L801.P$5, L802.P$3, L802.P$4, L802.P$5, R803.P$2 (2), R804.P$2 (2), R807.P$2 (2), R810.P$2 (2), R813.P$2 (2), R814.P$1 (1), R816.P$2 (2), U801.P$10 (GND), U801.P$25 (GND); also elsewhere on the board
unnamed: C807.P$1 (1), R805.P$2 (2), R806.P$1 (1), U801.P$1 (UV1)
unnamed: R806.P$2 (2), R807.P$1 (1), U801.P$2 (OV1)
unnamed: C808.P$1 (1), R808.P$2 (2), R809.P$1 (1), U801.P$3 (UV2)
unnamed: R809.P$2 (2), R810.P$1 (1), U801.P$4 (OV2)
unnamed: R812.P$2 (2), R813.P$1 (1), U801.P$6 (OV3)
unnamed: C809.P$1 (1), R811.P$2 (2), R812.P$1 (1), U801.P$5 (UV3)
unnamed: RN801.2 (1), U801.P$9 (!VALID3)
unnamed: C804.P$1 (1), U801.P$18 (VS1), U802.P$1 (S), U802.P$3 (S)
unnamed: L802.P$2, R802.P$2 (2)
unnamed: L801.P$2, R801.P$2 (2)
unnamed: R814.P$2 (2), U801.P$24 (HYS)
unnamed: C805.P$1 (1), U801.P$16 (VS2), U803.P$1 (S), U803.P$3 (S)
unnamed: C806.P$1 (1), U801.P$14 (VS3)
unnamed: U801.P$15 (G2), U803.P$2 (G), U803.P$4 (G)
unnamed: U801.P$17 (G1), U802.P$2 (G), U802.P$4 (G)
VBUS: R811.P$1 (1), U801.P$19 (V3)
VDD_5V_BRICK: C801.P$1 (1), J801.1, J801.2, R805.P$1 (1), U801.P$21 (V1), U802.P$7 (D), U802.P$8 (D); also elsewhere on the board
VDD_5V_IN: C803.P$1 (1), R815.P$2 (2), RN801.5 (2), RN801.6 (2), RN801.7 (2), U801.P$12 (VOUT), U802.P$5 (D), U802.P$6 (D), U803.P$5 (D), U803.P$6 (D); also elsewhere on the board
VDD_5V_SENS: R815.P$1 (1), R816.P$1 (1); also elsewhere on the board
VDD_SERVO: C802.P$1 (1), R808.P$1 (1), U801.P$20 (V2), U803.P$7 (D), U803.P$8 (D); also elsewhere on the board

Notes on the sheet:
Power source selector
Resistors picked so that undervoltage lockout starts at 4.0V and overvoltage lockout at 5.75V. Use 1% or better accuracy!
POWER PATH CONTROLLER: Does enable output if valid for continous 256 ms
XXX Check all input pins are 5V tolerant. Hooking this up to a 3.3V rail would make the lines non-readable during power-up sequencing

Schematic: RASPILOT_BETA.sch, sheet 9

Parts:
!VDD_BRICK_VALID: PAD.04; PAD.04X.04; PARTNO *
!VDD_SERVO_VALID: PAD.04; PAD.04X.04; PARTNO *
GND, GND.: PAD.04; PAD.04X.04; PARTNO *
IO-BOOT0: PAD.04; PAD.04X.04; PARTNO *
JP1, JP2: FIDUCIAL1.5X3; FIDUCIAL-1.5X3; PARTNO *
M3_MOUNT1101, M3_MOUNT1102, M3_MOUNT1103, M3_MOUNT1104: MOUNT-HOLE3.1MM; MOUNT-HOLE3.1; PARTNO *
OSHW_LOGO: OSHW-LOGOS; OSHW-LOGO-S; PARTNO *
RPI_AUX_ADC: PAD.04; PAD.04X.04; PARTNO *
S1RX, S1TX: PAD.04; PAD.04X.04; PARTNO *
VDD_3V3, VDD_5V_BRICK, VDD_5V_IN: PAD.04; PAD.04X.04; PARTNO *
VDD_SERVO: PAD.04; PAD.04X.04; PARTNO *

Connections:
!VDD_BRICK_VALID: !VDD_BRICK_VALID.P$1; also elsewhere on the board
!VDD_SERVO_VALID: !VDD_SERVO_VALID.P$1; also elsewhere on the board
GND: GND.P$1, GND..P$1; also elsewhere on the board
IO-BOOT0: IO-BOOT0.P$1; also elsewhere on the board
RPI-VDD_3V3: VDD_3V3.P$1; also elsewhere on the board
RPI_AUX_ADC1: RPI_AUX_ADC.P$1; also elsewhere on the board
SERIAL1_RX: S1RX.P$1; also elsewhere on the board
SERIAL1_TX: S1TX.P$1; also elsewhere on the board
VDD_5V_BRICK: VDD_5V_BRICK.P$1; also elsewhere on the board
VDD_5V_IN: VDD_5V_IN.P$1; also elsewhere on the board
VDD_SERVO: VDD_SERVO.P$1; also elsewhere on the board

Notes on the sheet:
Mounting holes to suit M3 fastener
and Richco R908 series spacer.
Use R908-5 spacers to stack with
other PX4 series boards (7.95 mm).
Production Testing Pads
Test and Fiducials
Minimum drill: 0.3 mm
Minimum trace width (use mm for traces): 0.15 mm
Minimum copper distance (all signals): 0.15 mm
Dimension / hole minimum distance: 0.2 mm
Layout grid: 4 mil, part grid: 4 mil. Dimensions / hole positions: 0.5 mm
Board: FR4 black, 1.0 mm. Solder stop on vias < 0.6 mm.
Signoff rules: Footprint checked, pinmap checked, schematic checked, cross-references to other pages checked.
Routing: 1: general/escape 2: ground 3: horizontal 4: vertical 5: power 6: general/escape
Fiducials for machine vision alignment.
Parts: Resistors: 0402 / 1% unless specified otherwise Capacitors: 0402 to 1206, ceramic, voltage rating: 10V unless specified
COMMS
POWER
STATUS AND ANALOG



Board: 4 copper layers, 65.1 x 56.0 mm, 169 parts (3 on the bottom side), 135 nets.

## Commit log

2015-05-23 new file: RASPILOT_BETA.brd new file: RASPILOT_BETA.sch
    [RASPILOT_BETA.brd, RASPILOT_BETA.sch]
2015-07-09 new file: RASPILOTv1_0.brd new file: RASPILOTv1_0.sch
    [RASPILOTv1_0.brd, RASPILOTv1_0.sch]
2015-08-12 new file: RASPILOTv1_0.pdf new file: RASPILOTv1_1.brd new file: RASPILOTv1_1.pdf new file: RASPILOTv1_1.sch
    [RASPILOTv1_1.brd, RASPILOTv1_1.sch]

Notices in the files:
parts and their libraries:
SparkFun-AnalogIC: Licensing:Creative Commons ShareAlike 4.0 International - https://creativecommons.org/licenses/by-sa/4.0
